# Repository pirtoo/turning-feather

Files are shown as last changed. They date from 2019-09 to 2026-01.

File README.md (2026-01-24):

# turning-feather
## Turning controller based on an Adafruit [Feather HUZZAH32](https://www.adafruit.com/product/3405) or [Feather ESP32 V2](https://www.adafruit.com/product/5400)

# This branch

This branch is testing LVGL and associated GUI libraries and a major restructuring of the code.
WiFi connectivity is working, it will create its own WiFI network if it cannot connect elsewhere.
LVGL display with dropdowns for program and stage selections, progress bars for the current exposure/away and for the stage as a whole are working.

Either disable WiFi or set a password on the WiFi network and an admin password on settings change.
There is a config menu on the device to reset settings if they are forgotten, to disable WiFi entirely and a signal strength meter for the ZPT RF remote control.

Still to come are popup messages for any errors or WiFi issues and if the ZPT remote control is low on battery or is not properly paired.

## Features

* More flexible than an [Auto Duel](https://web.archive.org/web/20170504011814/http://www.indelfa.co.uk/tt/ttcontruk.html) controller (and indelfa seem to have vanished), programs defined in JSON in a text file on a micro SD card. Can have a backup config file flashed to SPI accessed via LittleFS.

  * Current maximums of approx 55 programs and up to 12 stages per program (limited by memory in the controller) but will increase with development and it will be easier to swap between sets of programs.

  * [Example config](data/turnconf.txt).

  * Configs can be checked for JSON validity [here](https://arduinojson.org/v7/assistant/) or on any JSON website with a checker.

* Touch screen to select program/stage and start/stop face/away.

* RF remote control via [RF Solutions](https://www.rfsolutions.co.uk/) [ZPT module](https://www.rfsolutions.co.uk/radio-modules/zpt-433-868mhz-radio-telemetry-modules/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), compatable with their 4 button [Fobber](https://www.rfsolutions.co.uk/remote-control-systems/fobber-433mhz-868mhz-remote-control-key-fob-transmitter/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) or longer range [Trap](https://www.rfsolutions.co.uk/remote-control-systems/trap-handheld-transmitters-868mhz-or-918mhz-versions/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) remote.

  Remote buttons give:
  * start/stop
  * face/away
  * stage -
  * stage +

  You can set a program and walk down range without needing to return to the unit to run, stop or change stages. The buzzer chirps briefly by default when changing stage from the RF remote so if you are unsure which stage you are in you can go to the first or last stage (when it cannot go further so will not chirp) to establish what stage is set.

  ZPT module can be programmed to respond to several different remotes. See the [ZPT datasheet](https://www.rfsolutions.co.uk/content/download-files/ZPT-3-DATASHEET.pdf) for programming instructions. I keep the learning button internal to the unit so it can't be accidentally activated.

* Display is a [Featherwing 2.4" TFT](https://www.adafruit.com/product/3315) or [Featherwing 2.4" TFT V2](https://www.adafruit.com/product/3315).

* Optional WiFi control, with no configuration and with WiFi enabled the controller will create a WiFi network called `TurningFeather`. Connecting to that network with no password and connecting to `http://192.168.4.1/` will get you to the control page. `http://192.168.4.1/wifisetup.html` will allow you to change setup of network names and joining an existing WiFi network. The MAC address for the controller is displayed on the setup page and also over serial console while booting for setting ststic
IP addresses on your router or IP can be set on the device (not recommended). Pages like `wifisetup.html` can be protected by an admin password (default username is `admin`) but this is all sent over unencrypted HTTP so is not high security, just to keep prying fingers out.

* Control/power connector is RJ45; takes ground, +12V power and two signal lines for face and away activation at 12V. As used [here](https://web.archive.org/web/20190102055407/http://www.indelfa.co.uk/tt/tt_images/relay.gif).  The control and power connections are exposed to another optional board connector if you do not want to use a PCB mounted RJ45.

* [Parts list and assembly details](PCBs/README.md).

## Current state

* Software build and flash [managed by PlatformIO](platformio.md) for different versions of ESP32 and display boards.

* [Custom PCB](PCBs/kicad/turning-feather) made for the main IO board manufactured by [PCBWay](https://www.pcbway.com/project/shareproject/Turning_Feather.html). See [schematic](PCBs/kicad/turning-feather/turning-feather.pdf).

* New generation of graphics are in progress.

* Two physical buttons for face/away and start/stop. Program selection via the touchscreen. Start/stop, face/away and stage +/- via RF remote.

* If `USE_ZPT_SERIAL` is enabled the controller detects when it receives a packet from a remote that is not paired with the comntroller and displays a `?` character in the top right hand corner of the display. Similarly if the battery in the transmitter is low then it will display a `!` character. These characters clear the next time the controller receives a packet from a paired receiver that does not have a low battery.

* With an ESP32 V2 there is a Neopixel LED on the board, if enabled by default this will light up white during initial setup and Red/Green/Blue for beep/face/away during stages. It points backwards but if using the case with a mostly clear front it should be visible to see what part of a stage the unit is in and if it has finished from further away. This can be enabled/disabled with the `ESP_V2_NEOPIXEL` macro and the overall brightness set with `ESP_V2_NEOPIXEL_BRIGHTNESS`

* Spare 5v output for light flash or other features.

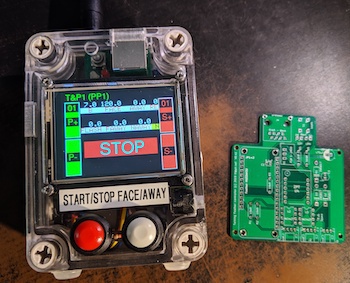
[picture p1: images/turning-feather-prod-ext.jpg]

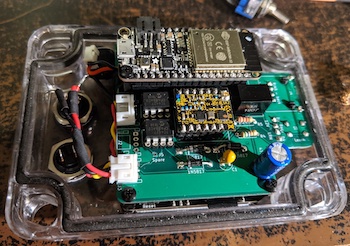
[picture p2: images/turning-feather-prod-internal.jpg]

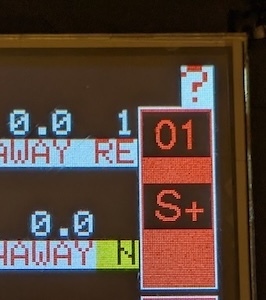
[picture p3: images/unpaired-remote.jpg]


## Future plans

Turning Feather is still very much in alpha and under development however it has been in use at one club for over 6 years.

- [ ] Config GUI to change system settings.

- [ ] Signal strength meter for the RFSolutions system.

- [ ] Add a stage name/comment to describe what each stage is for.

- [X] The [Feather HUZZAH32](https://www.adafruit.com/product/3405) microcontroller includes wifi, this will be used for setup, programming and control.

- [ ] Ability to change which config file is in use.

- [X] Updates planned here to provide [parts lists](PCBs/README.md), links, etc, to allow others to build their own units.

- [ ] Provide a full definition of the config file and what all the options do.

- [ ] Add random range options for configs for face/away times.

- [ ] Add the ability to use cheaper 433MHz radio transmitters (there are some nice 4/6 button units available) as an option but getting reliable detection of events with debouncing is hard to do well, unlike with the [RF Solutions](https://www.rfsolutions.co.uk/) units.

- [X] Support for the V2 versions of Adafruit Feather/Featherwing products used.

Other TODOs in the code are noted in the [main ino file](arduino/turning/turning.ino).

No plans to sell pre-made units in any volume but I may have one spare to sell that has not been installed in a case.

## Pull requests invited.

Feature request also invited.

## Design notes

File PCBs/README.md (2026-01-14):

# turning feather PCB and build

## Parts list to assemble with PCB

| Part | Quantity | Source |
| ---- | --- | --- |
| Capacitors |
| 0.1uF | x1 | |
| 22uF | x1 | |
| 470uF | x1 | |
| Resistors |
| 560R | x1 | |
| 2.2kR | x1 | |
| 10kR | x4 | |
| Diodes |
| 3mm LED | x2 | |
| 1N5817 | x4 | https://uk.farnell.com/stmicroelectronics/1n5817/diode-schottky-1a-20v-do-41/dp/9801197 |
| Connectors and cables |
| Socket headers | x1 pack | https://thepihut.com/products/36-pin-swiss-female-socket-headers-pack-of-5 |
| JST-PH 3 way PCB 90 degree | x1 | https://thepihut.com/products/jst-ph-jumper-assembly-3-wire |
| JST-PH 3 way plug and cable | x1 | Included in above |
| JST-PH 4 way PCB 90 degree | x1 | https://thepihut.com/products/jst-ph-jumper-assembly-4-wire |
| JST-PH 4 way plug and cable | x1 | Included in above |
| RJ45 PCB Shielded | x1 | https://uk.farnell.com/wurth-elektronik/615008142621/rj45-conn-r-a-jack-8p8c-1port/dp/2827822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 |
| Panel Mount Extension USB Cable | x1 | [For Feather V1](https://thepihut.com/products/panel-mount-extension-usb-cable-micro-b-male-to-micro-b-female) [for V2](https://shop.pimoroni.com/products/right-angle-panel-mount-extension-cables-25cm?variant=32013609664595) |
| SMA to uFL cable | x1 | https://thepihut.com/products/sma-to-ufl-u-fl-ipx-ipex-rf-adapter-cable or included with antenna |
| SMA antenna | x1 | https://thepihut.com/products/lora-antenna-with-pigtail-868mhz-black |
| Adafruit Stacking Headers for Feather | x1 | https://thepihut.com/products/stacking-headers-for-feather-12-pin-and-16-pin-female-headers |
| Switches |
| Panel mount DPDT toggle switch | x1 | https://www.adafruit.com/product/3220?srsltid=AfmBOopktvlaYSxf00hTX3HSPP8zWhvR285GFbeFXXPOa2BU2tYauQCs |
| 6mm PCB button | x1 | https://thepihut.com/products/metal-ball-tactile-button-6mm-x-10-pack |
| Panel mount push buttons | x2 | https://thepihut.com/products/12mm-domed-push-button-6-pack |
| Boards and ICs | | |
| Feather ESP32 | x1 | [V1](https://thepihut.com/products/adafruit-huzzah32-esp32-feather-board-pre-soldered-ada3591) [V2](https://thepihut.com/products/adafruit-esp32-feather-v2-w-fl-antenna-8mb-flash-2-mb-psram-stemma-qt) |
| TFT FeatherWing - 2.4" 320x240 | x1 | [V2](https://thepihut.com/products/adafruit-tft-featherwing-2-4-320x240-touchscreen-for-all-feathers) |
| ZPT receiver DIP 868Mhz | x1 | https://www.rfsolutions.co.uk/radio-modules/zpt-433-868mhz-radio-telemetry-modules/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 |
| TSR 1-2450 | x1 | https://uk.farnell.com/tracopower/tsr-1-2450/converter-dc-dc-5v-1a-sip/dp/1696320 |
| 4427 mosfet driver DIP-8 | x2 | https://uk.farnell.com/maxim-integrated-products/max4427epa/mosfet-driver-high-low-side-dip/dp/2516370 |
| Other |
| PCB | x1 | https://www.pcbway.com/project/shareproject/Turning_Feather.html |
| Remote control 868Mhz 4 buttons | x1 | https://www.rfsolutions.co.uk/remote-control-systems/fobber-433mhz-868mhz-remote-control-key-fob-transmitter/ or https://www.rfsolutions.co.uk/remote-control-systems/trap-handheld-transmitters-868mhz-or-918mhz-versions/ |
| 5v buzzer | x1 | https://thepihut.com/products/buzzer-5v-breadboard-friendly |
| M2.5 plastic standoff kit | x1 | https://thepihut.com/products/adafruit-black-nylon-screw-and-stand-off-set-m2-5-thread |
| Case Grey ABS Box Clear Lid 150x80x76 | x1 | https://thepihut.com/products/small-plastic-project-enclosure-weatherproof-with-clear-top |
| LiPo backup battery | x1 | https://thepihut.com/products/150mah-3-7v-lipo-battery |
| MicroSD card 1Gb-32Gb | x1 | |

One of the 1N5817 diodes should be inserted into the 5v supply line in the panel mount extension cable so when the unit has 12v supply, converting to 5V via the TSR 1-2450, this does not feed back to a USB connected device. 5v can be supplied either through the converter or from USB. If you do not install this diode I would not recommend connecting the controller to 12V and USB at the same time.

Input voltage is stated at 12v since this is what the original system uses. Minimum input voltage via the RJ45 is 6.5v and maxium input voltage is 36v to the TSR 1-2450. Maximum input voltage to the MAX4427EPA+ is 18v. Voltage output to the turn/away signals will be the input voltage.

The DPDT toggle switch turns the unit on and off and connects to J1 via the JST-PH 4 way cable. Pins 2 and 3 to each common on the switch, pin 1 to pin 2 in one position and pin 3 to pin 4 in the other position. In the off position 12v from the PCB RJ45 is not supplied back to the board and the enable pin of the Feather is grounded.

The two panel switches and the buzzer connect to J3 via the JST-PH 3 way cable. Pin 1 to the buzzer positive pin, pin 3 to the buzzer ground. Pin 2 to the first button and to a resistor to the second button and ground to the other button pins. This way when the button is pressed pin 2 is grounded directly, when the other button is pressed pin 2 is grounded via the resistor.

With the HUZZAH32/ESP32 you cannot read analog inputs on ADC #2 once WiFi has started as it is shared with the WiFi module. This pin is used as a digital input from the radio receiver so this should not cause problems. Maximum current output from each output pin is 1.1 mA, hence running the buzzer through a mosfet driver.

## Options

The LiPo battery to connect to the Feather is optional, a small battery is useful for using the controller when not connected to the target system and in case power is temporarily interrupted. A small battery will fit under the Feather board and connect to it.

Instead of using a PCB mounted RJ45 connector the optional J2 connector can be used to connect to 12v supply, ground, and turn/away signals. If you are not using J2 there is no need to fit a connector.

If you do not need a buzzer then U3 can be left off. The output will still flash the onboard LED by default. J3 pin 2 can be left unconnected.

# Assembly

Be careful to orient diodes, LEDs and tantalum/electrolytic capacitors correctly.

Note that some components (RJ45, LEDs and learn button) are placed on the rear side of the PCB.

The ZPT antenna is connected via the uFL connector on the ZPT board.

Plastic M2.5 standoffs should be used to mount the Featherwing display and HUZZAH32 to the IO board. Note that two of the mounting holes on the HUZZAH32 are partially obscured by the onboard 2.4GHz antenna so cannot be used.

V2 of the Adafruit ESP32 Feather is now supported as are V2 Adafruit display Featherwings, make sure to build the correct version for the hardware revisions you have. An ESP32 is required for the current code since it uses ESP32 timers.

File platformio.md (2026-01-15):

# turning-feather PlatformIO and code setup

## PlatFormIO

PlatformIO (used by me with Visual Studio Code) makes managing different build targets far simpler. The project now needs multiple build targets because the original Adafruit Feather ESP32 HUZZAH32 and Featherwing 2.4" TFT display have both been superseded with V2 version. You can still buy the V1 of the ESP32 but this may not continue, I have not found V1 displays still for sale.

All combinations of V1 and V2 ESP32 boards and display boards are supported by different targets in PlatformIO. The defines needed by the code to adapt for the different versions are included in the [platformio.ini](platformio.ini) config file.

One advantage of the V2 ESP32 board is you can buy a version with a connector for a larger WiFi antenna than the small built in antenna on V1 and other versions for the WiFi support.

Before making these changes I have created a [branch of the old Arduino IDE style setup](https://github.com/pirtoo/turning-feather/tree/last_arduino_ide) for reference.

## Display libraries

The project used to use TFT_eSPI but the configuration for it was not simple and outside the normal tree. The only reason I was using it was for nicer fonts and those fonts are now supported directly by Adafruit graphics libraries so I have switched over to those. PlatformIO will download the correct libraries via the [platformio.ini](platformio.ini) configuration.

## Internal filesystem

The boot splash image and the backup configuration live on internal flash,  LittleFS. The configuration is normally loaded from the sdcard and uses the internal filesystem as a backup in case there is no sdcard, the boot image is normally loaded from the internal filesystem.

If you use LittleFS the first time the ESP32 is powered on after the Turning Feather code is installed it will format the onboard filesystem then fail to load files from it since it is empty. You can then transfer the files in [data](data/) with [the Arduino IDE uploader](https://randomnerdtutorials.com/esp32-vs-code-platformio-littlefs/).

## ArduinoJson

The project has updated to ArduinoJson V7 which is current. This no longer needs a pre-calculation of size, it will work with json files up to the size of memory. If your json file doesn't work then it may be too large. A planned feature addition is the ability to use different files. Stage names are limited in length because the screen width is limited.

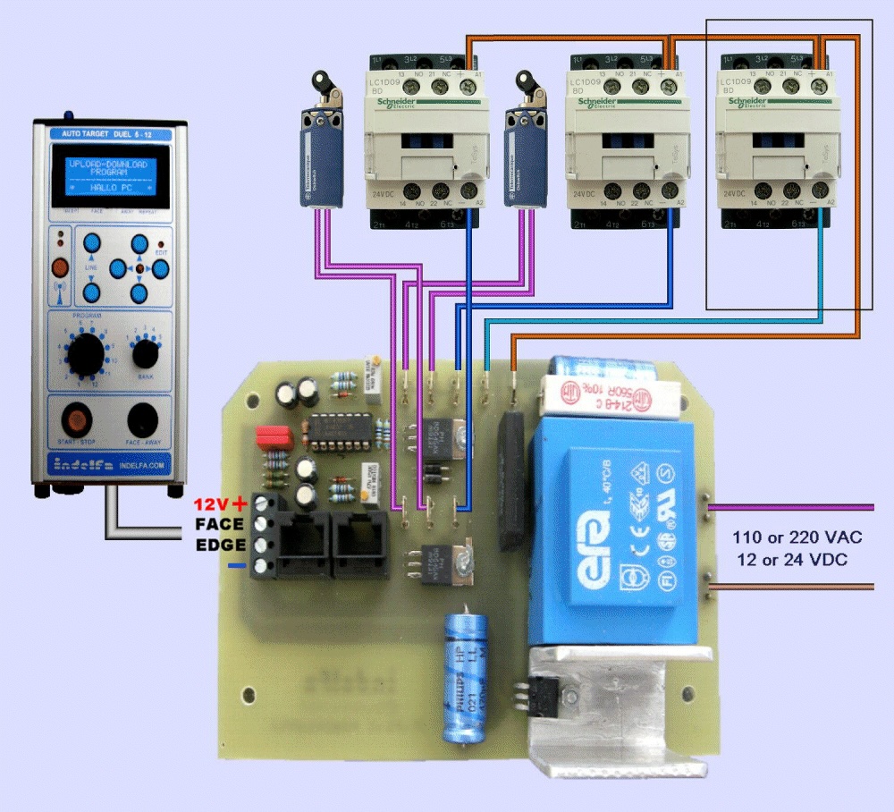
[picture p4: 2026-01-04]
images/indelfa-relay.jpg

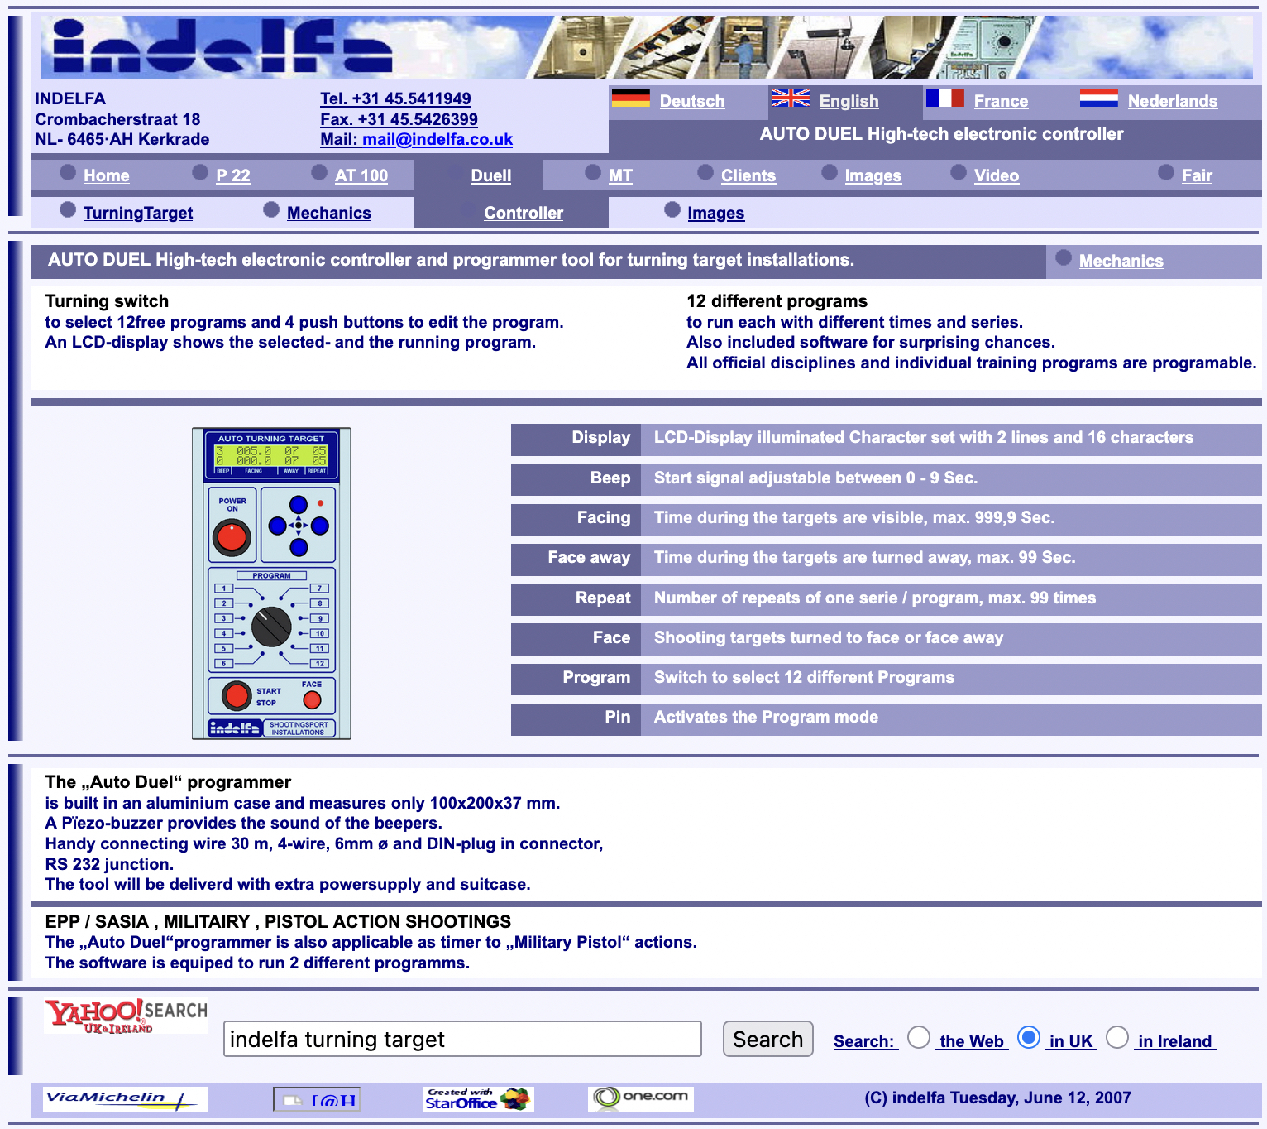
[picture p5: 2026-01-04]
images/indelfa-auto-duel.jpg

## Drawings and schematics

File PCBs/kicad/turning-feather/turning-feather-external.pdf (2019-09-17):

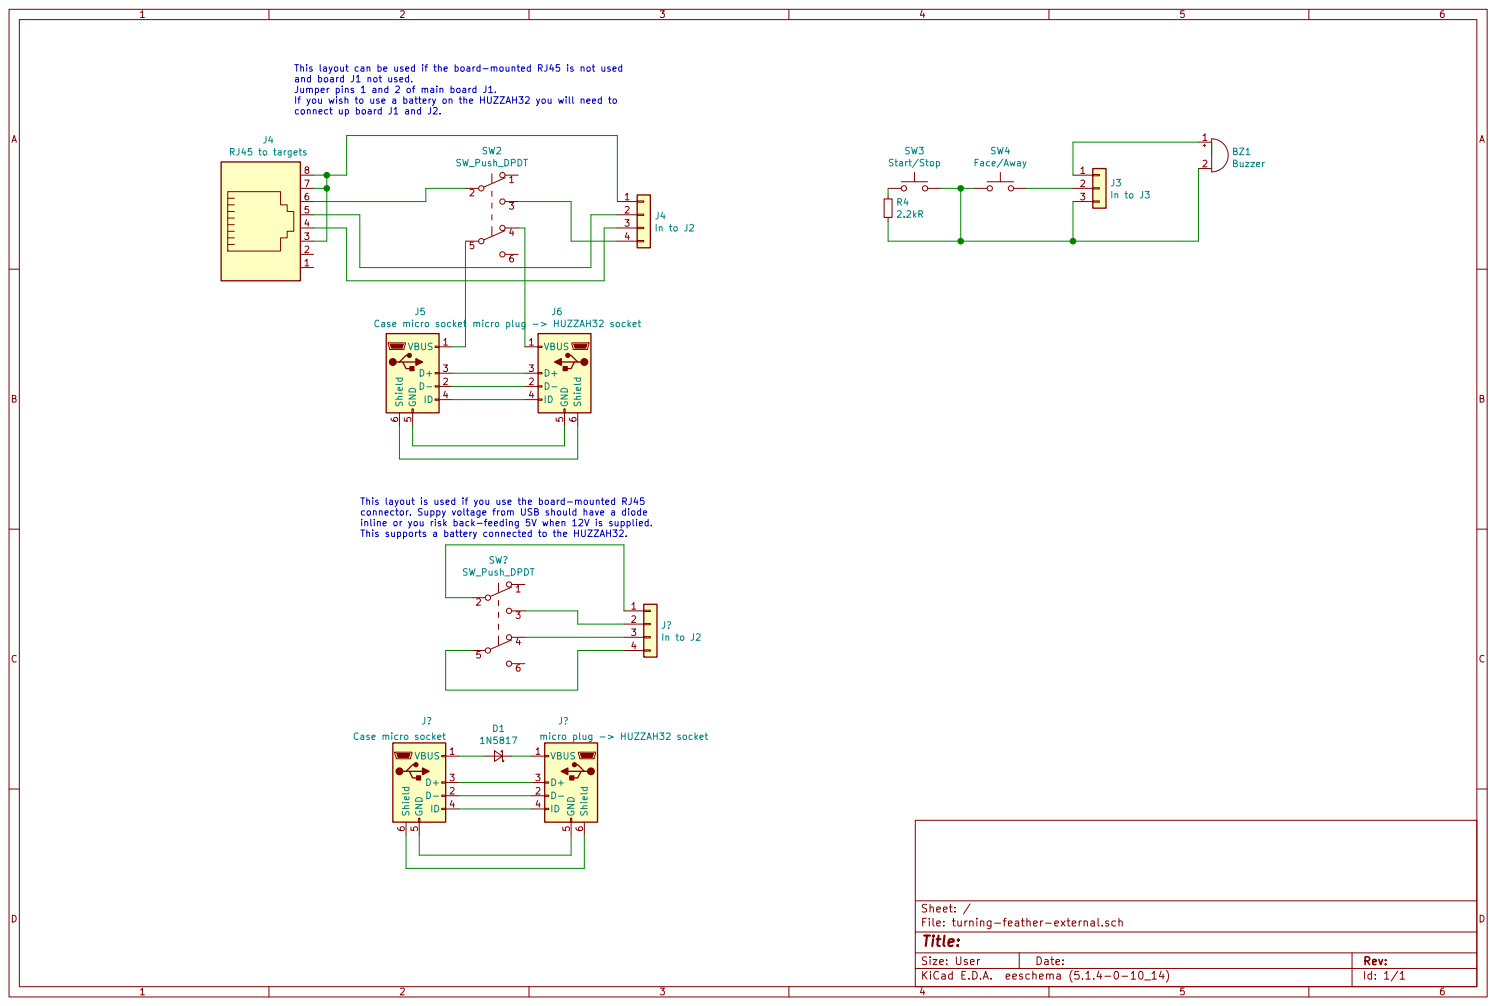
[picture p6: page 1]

J5 Case micro socket This layout can be used if the board-mounted RJ45 is not used
and board J1 not used. Jumper pins 1 and 2 of main board J1.

If you wish to use a battery on the HUZZAH32 you will need to
connect up board J1 and J2.

This layout is used if you use the board-mounted RJ45
connector. Suppy voltage from USB should have a diode
inline or you risk back-feeding 5V when 12V is supplied.
This supports a battery connected to the HUZZAH32.

File: turning-feather-external.sch Sheet: /
Id: 1/1 Title:

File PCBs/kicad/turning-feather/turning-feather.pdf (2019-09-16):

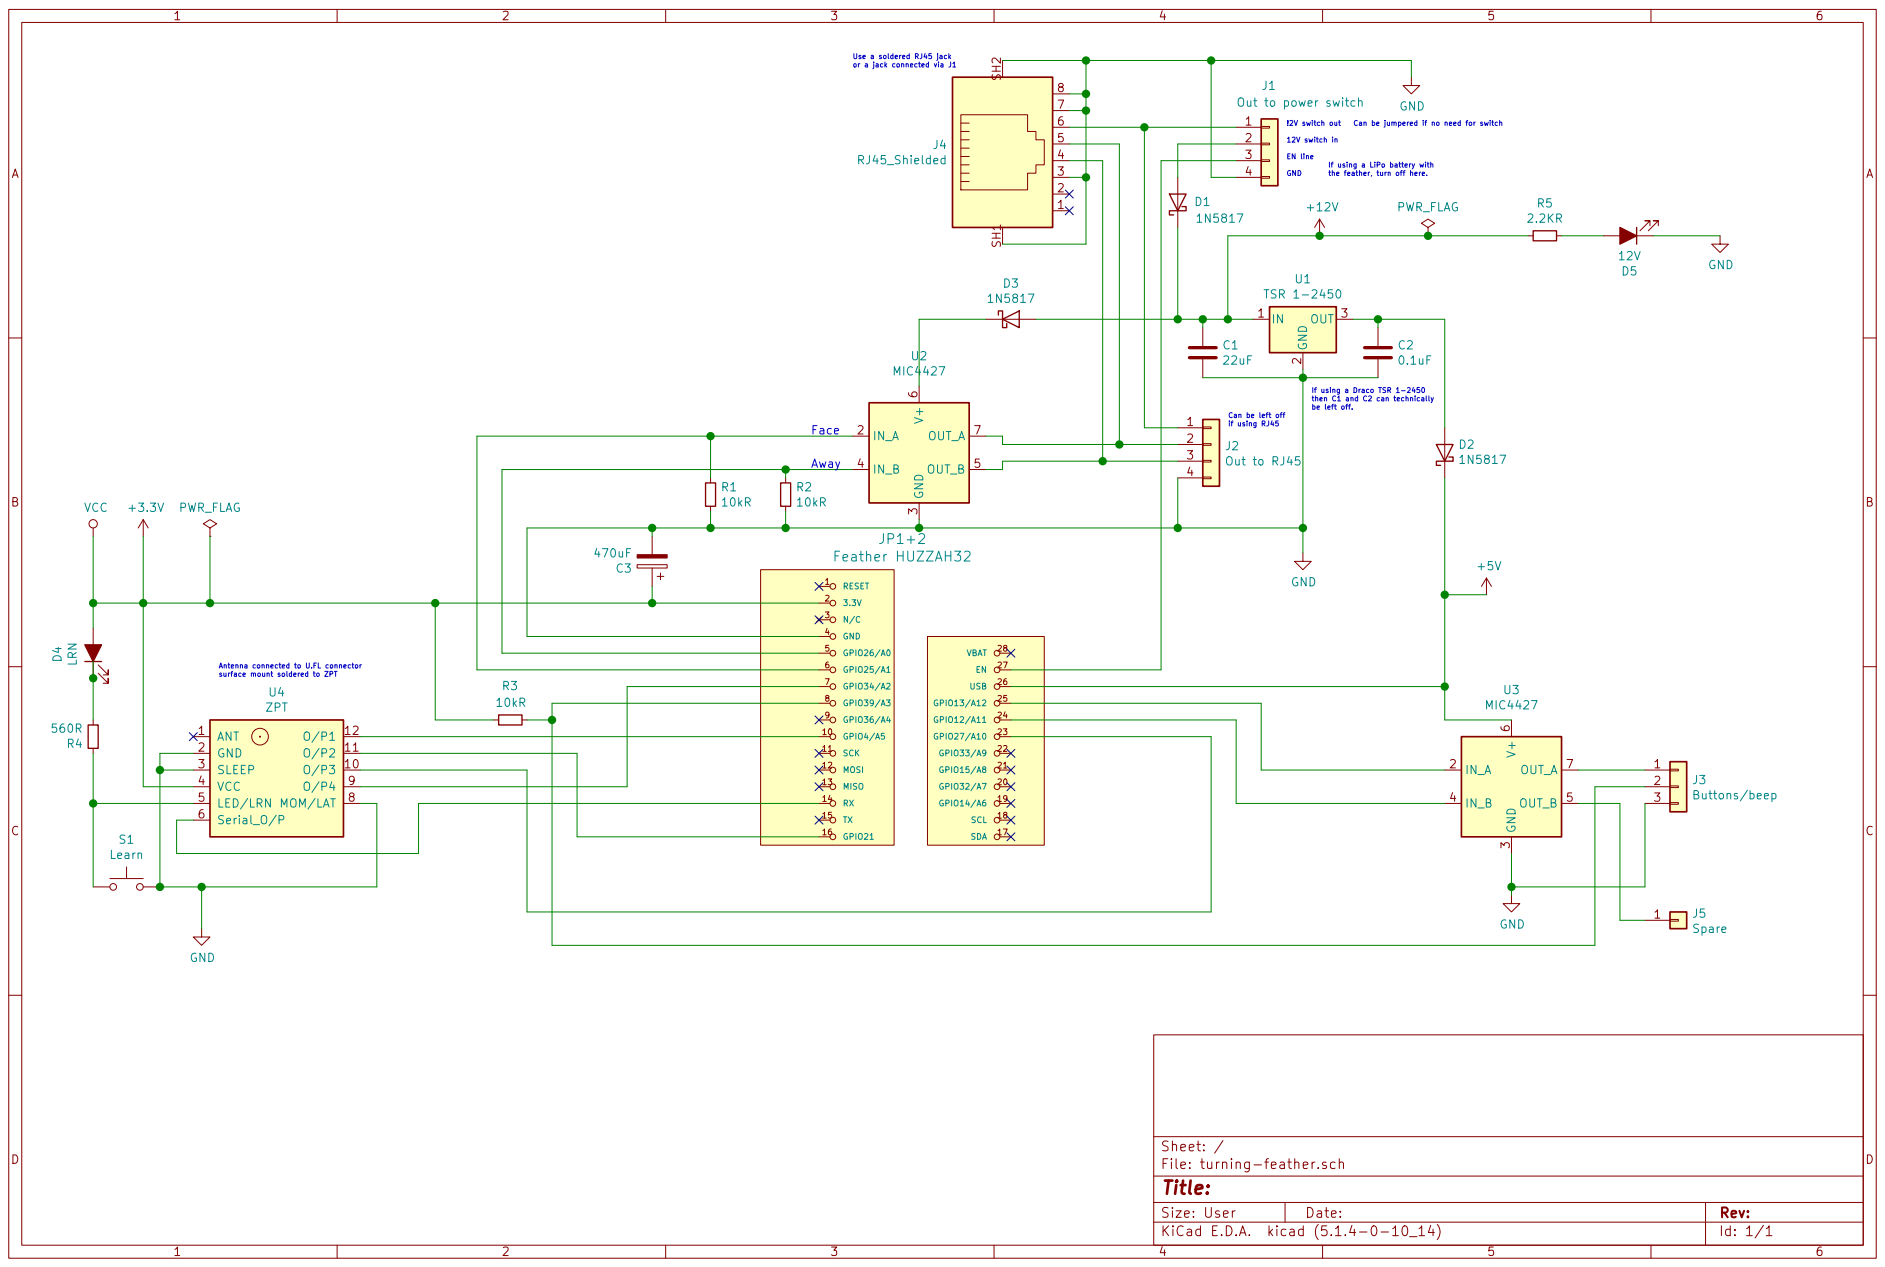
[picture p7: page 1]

If using a LiPo battery with
the feather, turn off here.

If using a Draco TSR 1-2450
then C1 and C2 can technically be left off.

if using RJ45 Face Away

Antenna connected to U.FL connector surface mount soldered to ZPT

GPIO4/A5 10 SCK 11 MOSI 12 MISO 13 RX 14 TX 15 GPIO21 16

File: turning-feather.sch Sheet: /

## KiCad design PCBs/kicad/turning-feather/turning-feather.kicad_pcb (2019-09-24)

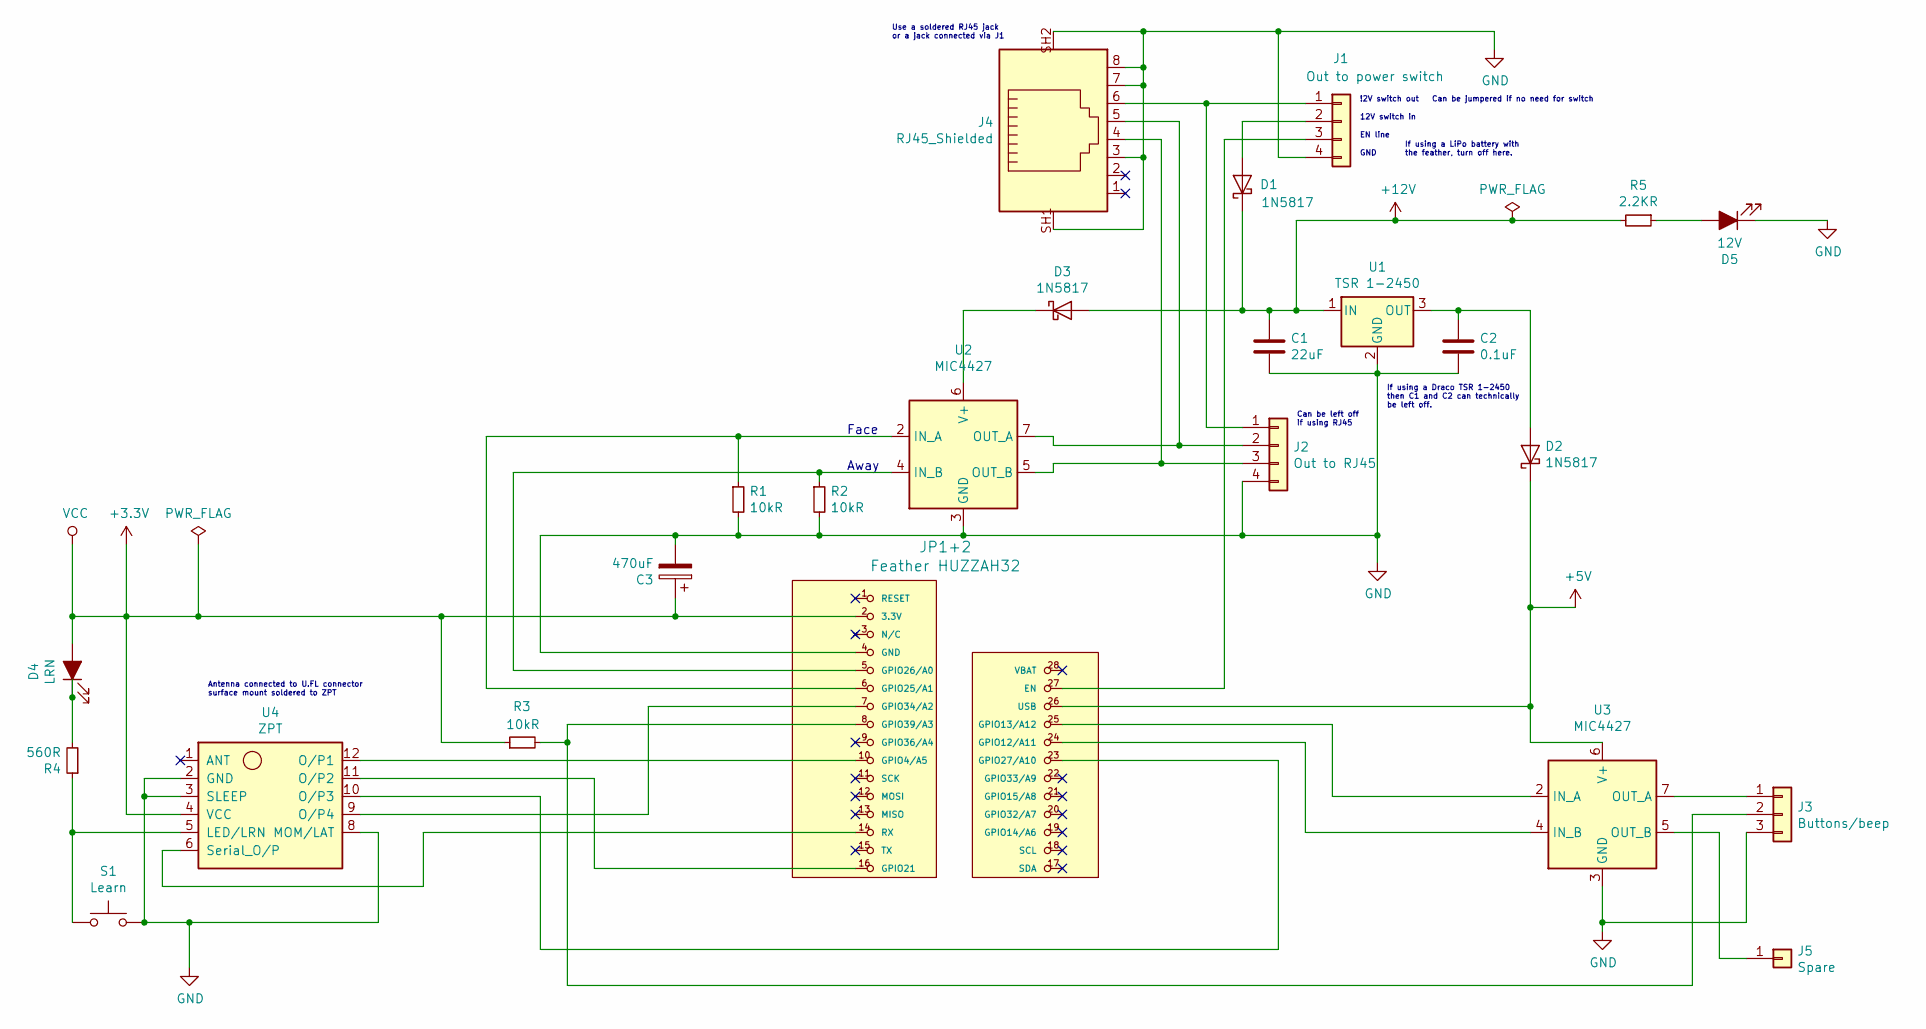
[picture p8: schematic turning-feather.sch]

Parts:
C1: 22uF; CP_Radial_Tantal_D4.5mm_P2.50mm
C2: 0.1uF; C_Disc_D3.0mm_W2.0mm_P2.50mm
C3: 470uF; CP_Radial_D6.3mm_P2.50mm
D1, D2, D3: 1N5817; D_DO-41_SOD81_P10.16mm_Horizontal
D4: LRN; LED_D3.0mm_Clear
D5: 12V; LED_D3.0mm_Clear
J1: Out to power switch; JST_PH_S4B-PH-K_1x04_P2.00mm_Horizontal
J2: Out to RJ45; JST_PH_S4B-PH-K_1x04_P2.00mm_Horizontal
J3: Buttons/beep; JST_PH_S3B-PH-K_1x03_P2.00mm_Horizontal
J4: RJ45_Shielded; RJ45_Horizontal_Shielded
J5: Spare; PinHeader_1x01_P1.00mm_Vertical
JP1+2: Feather HUZZAH32; ADAFRUIT_FEATHER
R1, R2, R3: 10kR; R_Axial_DIN0207_L6.3mm_D2.5mm_P7.62mm_Horizontal
R4: 560R; R_Axial_DIN0207_L6.3mm_D2.5mm_P7.62mm_Horizontal
R5: 2.2KR; R_Axial_DIN0207_L6.3mm_D2.5mm_P7.62mm_Horizontal
S1: Learn; SW_PUSH_6mm_H5mm
U1: TSR 1-2450; Converter_DCDC_TRACO_TSR-1_THT
U2, U3: MIC4427; DIP-8_W7.62mm
U4: ZPT; ZPT8RD

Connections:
+3V3: C3.1, D4.2 (A), JP1+2.2 (3.3V), R3.1, U4.4 (VCC)
+5V: D2.1 (K), JP1+2.26 (USB), U3.6 (V+)
+12V: C1.1, D1.1 (K), D3.2 (A), R5.2, U1.1 (IN)
GND: C1.2, C2.2, C3.2, D5.1 (K), J1.4, J2.4, J3.3, J4.3, J4.7, J4.8, J4.SH1, J4.SH2, JP1+2.4 (GND), R1.2, R2.2, S1.2, U1.2 (GND), U2.3 (GND), U3.3 (GND), U4.2 (GND), U4.3 (SLEEP), U4.8 (MOM/LAT)
unnamed: C2.1, D2.2 (A), U1.3 (OUT)
unnamed: D1.2 (A), J1.2
unnamed: D3.1 (K), U2.6 (V+)
unnamed: D4.1 (K), R4.2
unnamed: D5.2 (A), R5.1
unnamed: J1.1, J2.1, J4.6
unnamed: J1.3, JP1+2.27 (EN)
unnamed: J2.2, J4.5, U2.7 (OUT_A)
unnamed: J2.3, J4.4, U2.5 (OUT_B)
unnamed: J3.1, U3.7 (OUT_A)
unnamed: J3.2, JP1+2.8 (GPIO39/A3), R3.2
unnamed: J5.1, U3.5 (OUT_B)
unnamed: JP1+2.5 (GPIO26/A0), R2.1, U2.4 (IN_B)
unnamed: JP1+2.6 (GPIO25/A1), R1.1, U2.2 (IN_A)
unnamed: JP1+2.7 (GPIO34/A2), U4.9 (O/P4)
unnamed: JP1+2.10 (GPIO4/A5), U4.12 (O/P1)
unnamed: JP1+2.14 (RX), U4.6 (Serial_O/P)
unnamed: JP1+2.16 (GPIO21), U4.11 (O/P2)
unnamed: JP1+2.23 (GPIO27/A10), U4.10 (O/P3)
unnamed: JP1+2.24 (GPIO12/A11), U3.4 (IN_B)
unnamed: JP1+2.25 (GPIO13/A12), U3.2 (IN_A)
unnamed: R4.1, S1.1, U4.5 (LED/LRN)

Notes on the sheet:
Face
Away
If using a Draco TSR 1-2450 then C1 and C2 can technically be left off.
If using a LiPo battery with the feather, turn off here.
Antenna connected to U.FL connector surface mount soldered to ZPT
Use a soldered RJ45 jack or a jack connected via J1
Can be jumpered if no need for switch
Can be left off if using RJ45
!2V switch out
12V switch in
EN line
GND

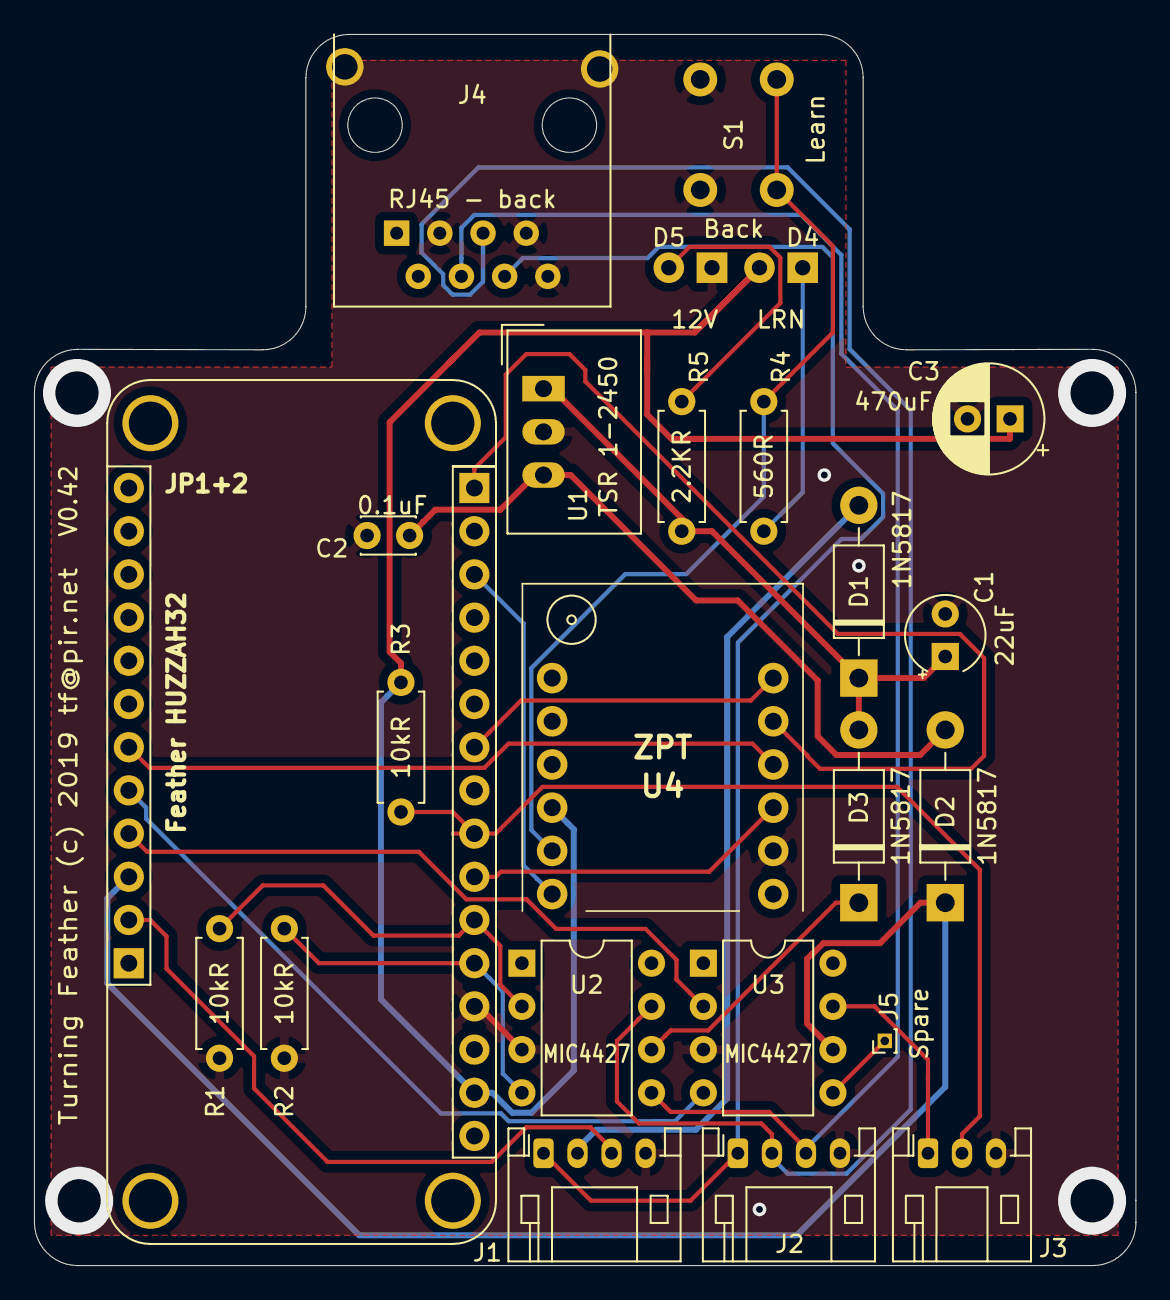
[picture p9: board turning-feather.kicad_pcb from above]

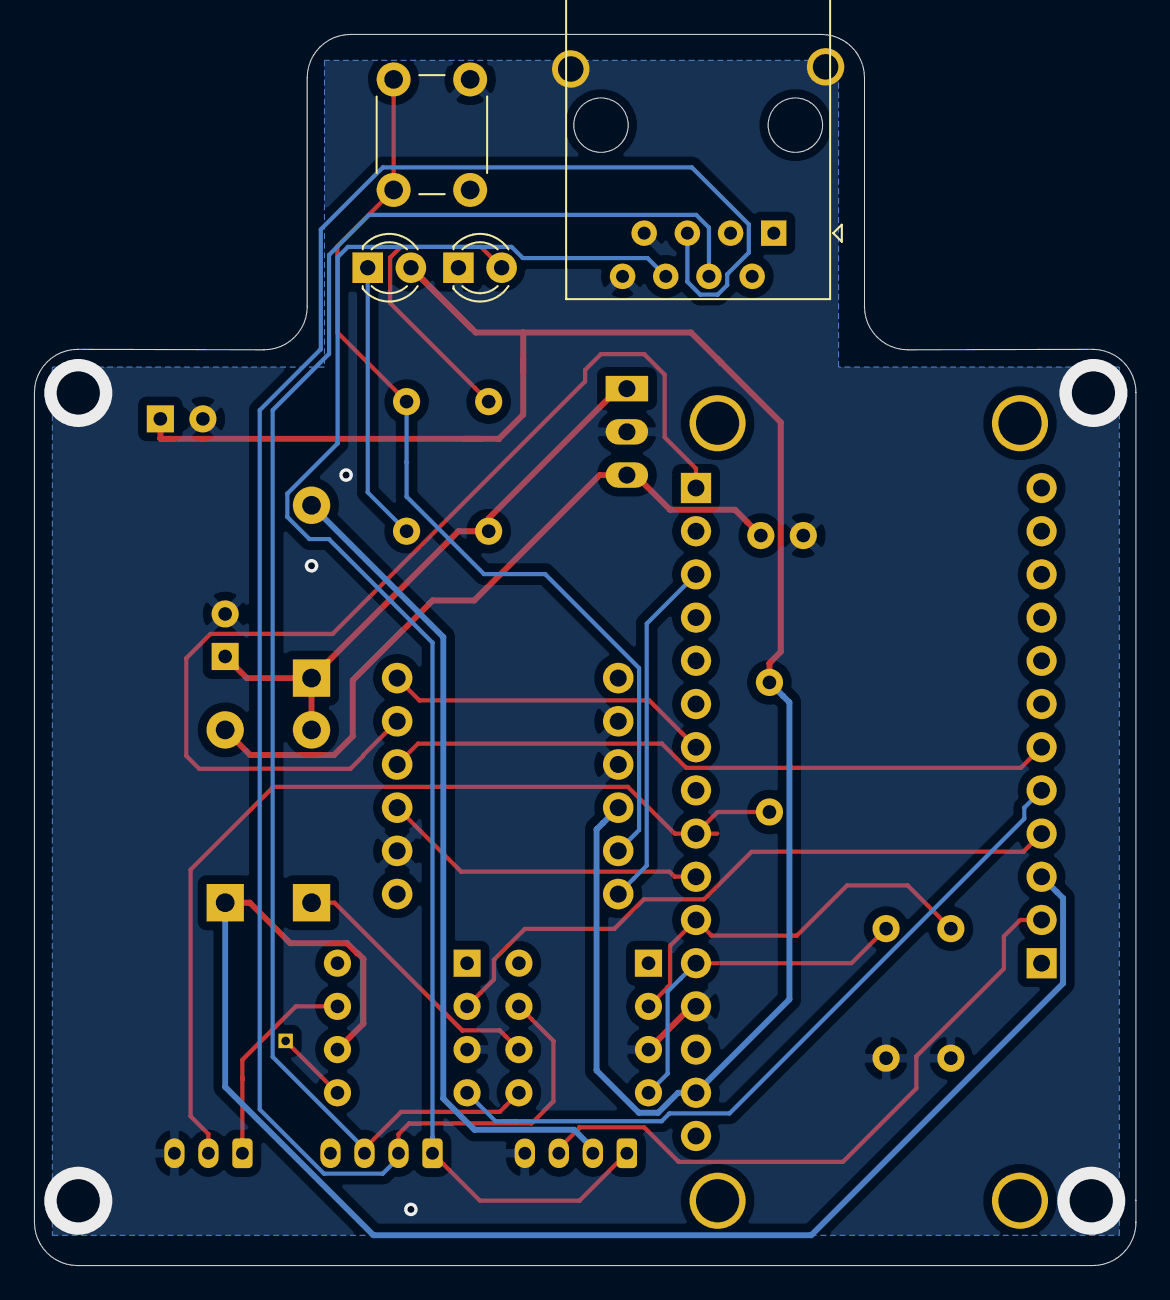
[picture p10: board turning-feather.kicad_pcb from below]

Board: 2 copper layers, 64.8 x 72.4 mm, 24 parts (4 on the bottom side), 26 nets.

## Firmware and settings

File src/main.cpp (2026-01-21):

/*
 * Turning target controller.
 * Turning feather.
 *
 * Set up for PlatformIO
 */


// TODO: Put fudge times into a config file
// TODO: Put chirp (and chirp time) into config file
// TODO: WIFI/web server
//       - edit device config file
//       - ability to edit extra configs
// TODO: add extra turning configs, concat them from
//         main file, write out seperately?
// TODO: Have a directory on SD let you choose config?
//       - or boot with face/away held down to choose
//         files?
// TODO: Text for stage use, eg: "GRCF stage 1"?
//       - will this make the file too large for json?


// General includes
#include <Arduino.h>
#include "main.h"
#include "turning.h"
#include "turn_tft.h"
#include "zpt_serial.h"
#include "sdcard.h"
#include "ui/vars.h"

bool config_mode=false;
unsigned long start_millis;

#if defined(FEATHER_ESP32_V2) && defined(ESP_V2_NEOPIXEL)
#include "turn_neopixel.h"
#endif //FEATHER_ESP32_V2 && ESP_V2_NEOPIXEL

#ifdef ZPT_BUTTONS
#include "turn_zpt_buttons.h"
#endif //ZPT_BUTTONS

#ifdef PHYSICAL_BUTTONS
#include "analogbuttons.h"
#endif // PHYSICAL_BUTTONS

// WiFi
#ifdef TURN_WIFI_ENABLE
#include "turn_wifi.h"
#endif //TURN_WIFI_ENABLE

#ifdef USE_ZPT_SERIAL
#include "zpt_serial.h"
void zpt_serial_actions();
void zpt_serial_actions() {
  if (zpt_packet_lowbatt()) {
    // Print a red on white '!' if remote battery low
    // TODO display element or popup?
    //lcd_statusprint('!');
  } else if (!zpt_packet_learn()) {
    // Print a red on white '?' if remote not paired
    // TODO dispay element?
    //lcd_statusprint('?');
  } else {
    // Clear status
    // TODO clear element
    //lcd_statusclear();
  }
  set_var_zpt_signal_strength_int(zpt_packet_rssi());
}
#endif //USE_ZPT_SERIAL

void set_config_mode(bool mode) {
  config_mode=mode;
}

// Setup everything that needs to be set up
void setup() {
  // outputs setup
  // Make aure the 12v mosfet drivers are off
  pinMode(FACE_PIN, OUTPUT);
  digitalWrite(FACE_PIN, LOW);
  pinMode(AWAY_PIN, OUTPUT);
  digitalWrite(AWAY_PIN, LOW);
  // Set up other general pins
  pinMode(BUZZER, OUTPUT);
  pinMode(UNUSED_1, OUTPUT);
  digitalWrite(BUZZER, LOW);
  digitalWrite(UNUSED_1, LOW);

  // Serial setup
  Serial.begin(SERIAL_SPEED);
  while (!Serial) {
    delay(100); // wait for serial port
  }
  // some delay before dealing with SPI, let it settle
  delay(1000);
  Serial.println("\r\nStart\r\n");
  Serial.println("Turning Feather");
  Serial.println("(c) pir 2019-2026");
  Serial.println("tf@pir.net\r\n");

#if defined(FEATHER_ESP32_V2) && defined(ESP_V2_NEOPIXEL)
  // Set up a Neopixel if configured.
  np_setup();
#endif //FEATHER_ESP32_V2 && ESP_V2_NEOPIXEL

  // If microsd doesn't work
  // Keep this before the display setup;
  //SPI.begin(SCK, MISO, MOSI, SD_CS_PIN);
  pinMode(SD_CS_PIN, OUTPUT);
  //SPI.setDataMode(SPI_MODE0);

#ifdef DEBUG
  Serial.println("Calling storage_init");
#endif //DEBUG
  // Keep this before the display setup
  storage_init();

#ifdef DEBUG
  Serial.println("Running setup_tft_screen");
#endif //DEBUG
  setup_tft_screen();

  //loadScreen(SCREEN_ID_SPLASH);
  //loop_tft_screen();

#ifdef USE_ZPT_SERIAL
#ifdef DEBUG
  Serial.println("Running zpt_serial_setup");
#endif //DEBUG
  // ZPT serial setup
  zpt_serial_setup();
#endif //USE_ZPT_SERIAL

  // Is the turn/face button being held down at boot?
  if (analogRead(BUTTONS_PIN) < 5) {
//  if (true) {
    set_config_mode(true);
    loadScreen(SCREEN_ID_CONFIG_MAIN);
  }

#ifdef DEBUG
  Serial.println("Running setup_turnconfig");
#endif //DEBUG
  // Load the config into a datastructure
  setup_turnconfig();

  // If enabled bring up WiFi
#ifdef TURN_WIFI_ENABLE
#ifdef DEBUG
  Serial.println("Calling initWifi");
#endif //DEBUG
  if (! initWifi()) {
    // WiFi init failed
    // TODO change this to a popup?
    lcd_println("WiFi disabled             ");
    delay(2000);
  }
#else //TURN_WIFI_ENABLE
  Serial.println("WiFi disabled, TURN_WIFI_ENABLE not defined");
#endif //TURN_WIFI_ENABLE

#ifdef PHYSICAL_BUTTONS
  // Physical buttons setup
#ifdef DEBUG
  Serial.println("Calling buttons_setup");
#endif //DEBUG
  buttons_setup();
#endif //PHYSICAL_BUTTONS

  // bravo/ZPT RF setup
#ifdef DEBUG
  Serial.println("Calling zpt_buttons_setup");
#endif //DEBUG
  zpt_buttons_setup();

  // Timer and face/away setup.
#ifdef DEBUG
  Serial.println("Calling timer_setup");
#endif //DEBUG
  timer_setup();

  Serial.println(F("\r\nSetup finished.\r\n"));
#if defined(FEATHER_ESP32_V2) && defined(ESP_V2_NEOPIXEL)
  np(0);
#endif //FEATHER_ESP32_V2 && ESP_V2_NEOPIXEL
  delay(2000);
}

void loop() {
  // Anything related to the screen/UI
  loop_tft_screen();

#ifdef TURN_WIFI_ENABLE
  wifiloop();
#endif //TURN_WIFI_ENABLE

  if (! config_mode) {
#ifdef ZPT_BUTTONS
    zpt_buttons_loop();
#endif // ZPT_BUTTONS

#ifdef PHYSICAL_BUTTONS
    // Physical buttons action
    buttons_loop();
#endif

    // Check semaphore and run turntick if ready
    turntick_loop();
  }

#ifdef USE_ZPT_SERIAL
  // ZPT serial handling
  zpt_serial_loop();
  if (zpt_packet_isready()) {
    zpt_serial_actions();
    // Signal ready for another packet.
    zpt_packet_getnew();
  }
#endif //USE_ZPT_SERIAL

  yield();
}

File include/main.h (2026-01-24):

/*
 * Turning target controller.
 * Turning feather.
 *
 * General definitions.
 */

#ifndef TF_MAIN_H
#define TF_MAIN_H


// Extra debugging to the serial port while running
//#define DEBUG
//#define DEBUG2
//#define DEBUG_TIMER

// Using the V2 version of the Adafruit ESP32, default is V1
//#define FEATHER_ESP32_V2
// If you have the ESP32 V2 you can use the built in NEOPIXEL
//#define ESP_V2_NEOPIXEL

// Using the V2 version of the Adafruit TFT 2.4" featherwing
//#define TSC2007_TS=1

// To use ESP32 WiFi
//#define TURN_WIFI_ENABLE

// Default config file, json, sdcard or LittleFS
#define TURNCONF "/turnconf.txt"

// Constants
// Clock rate for timer
#define CLOCK_RATE 100000
#define ONE_SECOND 100000
#define TENTH_SECOND 10000

// How long a start beep lasts
#define BEEP_LENGTH 0.8*ONE_SECOND
// How long to keep the motors going on a turn
#define CHANGE_LENGTH 0.4*ONE_SECOND
// Tenth of a second gives enough repeats to loop properly
#define TURN_RATE TENTH_SECOND

// Keep the face/away lines high while a stage is running
#define KEEP_CHANGE_ACTIVE

// Length of beep chirp when RF stage change happens
// Comment out to disable entirely
#define STAGE_CHANGE_CHIRP 0.4*TENTH_SECOND

// Fudge to allow time for targets to turn
// in 10ths of a second
#define BEEP_FUDGE 1
#define FACE_FUDGE 3
#define AWAY_FUDGE 3

// Number of tenths of seconds (TURN_RATE) from start
// until the targets are faced or the beep, depending
// on config.
#define INIT_PAUSE 6

// LED_BUILTIN is 13 on the HUZZAH32
#define BUZZER LED_BUILTIN

// Pins thst go to the mosfets to drive 12V turn/away
#define FACE_PIN 25
#define AWAY_PIN 26

// On Feather ESP32 V2 the physical board button is BUTTON/38

// Unused currently
// Double the value here to get battery voltage
//#define BATTERY_VOLTAGE A13

// Unused output on the HUZZAH32
#define UNUSED_1 12 // AKA A11, wired to 5v MOSFET
//#define UNUSED_2 A4/36

// Using these to generate rising edge interrupts fails badly.
//#define BAD_1 36
//#define BAD_2 39

// Serial speed
#define SERIAL_SPEED 115200

// Extra serial output from the ZPT
#define USE_ZPT_SERIAL
// Enable buttons on RF remote
#define ZPT_BUTTONS
// Enable physical buttons on case
#define PHYSICAL_BUTTONS

#define STR_IMPL_(x) #x
#define STR(x) STR_IMPL_(x)

// For core 3.0.0 and higher
#if ESP_ARDUINO_VERSION_MAJOR >= 3 && defined(ESP32)
  #include <driver/gpio.h>
  #include <rom/ets_sys.h>
#endif //ESP_ARDUINO_VERSION_MAJOR >= 3 && defined(ESP32)

void set_config_mode(bool mode);

#endif //TF_MAIN_H

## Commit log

2019-08-28 Initial set of arduino files and kicad files for turning feather
    [tft-feather-stripped.kicad_pcb, turning-feather-external.sch, turning-feather.kicad_pcb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]
2019-08-29 Reformat a print and add a TODO
2019-08-29 Add serial output from ZPT to serial in on feather. PCB V0.23.
    [turning-feather.kicad_pcb, turning-feather.sch]
2019-08-29 Update schematic with plotted pdf
2019-08-31 Add parsing of ZPT serial data and unify block comment styles
    The ZPT unit outputs a serial data packet format with information
    about received signal from a transmitter. If this is connected to Serial2
    on the feather HUZZAH32 we can parse it and get informaiton such as
    transmitter low battery or if the button has been learned by the
    receiver and print up a status character int the top right to warn the user
    '!' means low battery and '?' means unlearned button code.
2019-08-31 PCB version 0.32.
    Add serial connection from ZPT to Serial2 on HUZZAH32.
    Connect spare 5V MOSFET input to spare HUZZAH32 output with header.
    Add on-board PCB mount RJ45 as an option, old connector retained.
    Move LEDs out to new board extension back to point towards user.
    [turning-feather-0.23.kicad_pcb, turning-feather.kicad_pcb, turning-feather.sch]
2019-09-06 Move ethernet on-PCB, move most things around, change capacitors, etc
    [turning-feather.kicad_pcb, turning-feather.sch]
2019-09-07 Clean up filled areas a little
    [turning-feather.kicad_pcb]
2019-09-07 Some cleanup to pcb and schema
    [turning-feather.kicad_pcb, turning-feather.sch]
2019-09-08 Small cleanups for v0.41
    [turning-feather.kicad_pcb]
2019-09-10 Fix dimension markers to the new lower edge of the board
    [turning-feather.kicad_pcb]
2019-09-16 Move DIL base slightly over to provide room for header sockets to be used
    [turning-feather.kicad_pcb]
2019-09-16 Update external schematic with options
    [turning-feather-external.sch]
2019-09-16 Add schematic pdfs for current rev
2019-09-17 Fix some minor labelling issues
    [turning-feather.kicad_pcb]
2019-09-17 Label diode and add text to external schema
    [turning-feather-external.sch]
2019-09-18 Add some fudge horizontally for pressing screen buttons
2019-09-24 Slight tweaks for fitting
    [turning-feather.kicad_pcb]
2019-11-09 Update turning configuration read/write
    Default and minimum repeats is 1, enforcing display behaviour because
    it looks odd otherwise.
    Rename capacity variables to turn_capacity to allow for other configs
    (like system).
    Expand comments.
2019-11-09 Add ESP32 specific restart utility
2019-11-09 turning.ino updates for logic, etc
    Fix logic in not quite a state machine so states are not skipped
    through (wasting a tick and causing a flicker on the screen) if they
    are not going to be used (because the option is zero).
    Fix logic if autonext is set on the last stage in a program.
    ifdef out more ZPT serial sections if zpt serial is not used.
    Make sure timer stops when running stops.
    Comment and whitespace fixes
2019-11-09 Make sure last stage does not have autonext or nextaway set
2019-11-09 Clean up old versions and give an ignored directory to stash them
    [turning-feather-0.23.kicad_pcb]
2019-11-09 Add board version 0.42 gerber plots
2021-06-11 Remove the option for arduino gfx library because later options will require TFT_eSPI
2021-06-11 Simpligy change timer and give the option of keeping output lines high during a stage
2021-06-14 Link to replaecment 4 button Trap remote
2021-08-23 Fix link to display board
2025-12-30 Bring up to working with current versions of libraries and add a little more docs
2026-01-01 Add PCB/construction documentation
2026-01-02 Allow for Adafruit ESP32 V2 and streamline zpt serial use
2026-01-02 Correct docs about 12v via J2
2026-01-04 Move arduino to platformio locations
2026-01-04 Major rework to use platformio, support new boards and drop TFT_eSPI since adafruit default libraries now do nice fonts
    [sdcard.cpp, turning.cpp, zpt_serial.cpp]
2026-01-04 Add Neopixel support for ESP32 V2 boards
2026-01-06 First stage of WiFi support; creates a network or joins a network and can manage wifi settings over wifi.
2026-01-06 Rework to split a lot of things out of turning.cpp. Put setup() and loop() and other basics into main.cpp. Move neopixel to own files.
    [main.cpp, main.h, tf_wifi.cpp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]
2026-01-06 More refactorying, rf buttons to own file
2026-01-14 Fix edge case where a large number of failed connections return at once and button text did not update
2026-01-17 Fix MAC disoplay for local AP as well as remote wifi connection
    [turn_wifi.cpp]
2026-01-19 Add partition schemes for 4 and 8mb boards
    [default_4MB.csv, default_8MB.csv, no_ota_4MB.csv]
2026-01-21 Major restructure, addition of LVGL and EEZ libraries. Not finished yet, stage info is not displayed on screen.

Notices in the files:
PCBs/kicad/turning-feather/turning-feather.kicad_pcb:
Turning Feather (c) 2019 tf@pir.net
